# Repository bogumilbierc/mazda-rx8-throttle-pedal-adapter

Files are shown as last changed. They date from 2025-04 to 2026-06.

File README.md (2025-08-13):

# Mazda RX-8 throttle pedal to M113 ECU adapter

Mazda RX-8 throttle pedal adapter for Mercedes M113 ECU (M113 V8 swap into RX-8).

<!-- TOC -->
* [Mazda RX-8 throttle pedal to M113 ECU adapter](#mazda-rx-8-throttle-pedal-to-m113-ecu-adapter)
  * [OEM Pedals documentation](#oem-pedals-documentation)
  * [Adapter](#adapter)
    * [How it works](#how-it-works)
    * [Basic logic (runs in loop)](#basic-logic-runs-in-loop)
  * [Components](#components)
  * [Circuit diagram](#circuit-diagram)
  * [Assembled adapter](#assembled-adapter)
  * [Arduino IDE setup](#arduino-ide-setup)
  * [Adopting a similar solution for other swaps (different ECUs/pedals)](#adopting-a-similar-solution-for-other-swaps-different-ecuspedals)
<!-- TOC -->

## OEM Pedals documentation

- [RX-8 pedal](./docs/rx-8-pedal/rx-8-pedal.md)
- [M113 pedal](./docs/m113-pedal/m113-pedal.md)

## Adapter

### How it works

Mazda RX-8 pedal has two sensors (potentiometers) that have voltage offset between each other.

M113 pedal has two sensors (potentiometers) that have one sensor being 2*voltage of the other sensor.

Adapter reads the voltage from Mazda pedal, converts it to M113 voltage with DAC (for one sensor) and then takes output
from DAC and divides it by two using a simple resistor-based voltage divider for the other sensor.

### Basic logic (runs in loop)

1. Read voltages from both sensors on RX-8 pedal
2. Calculate percentage from both sensors
3. Validate if percentages are not out of sync (safety feature)
    - if they are, set the throttle limit to 30%
    - if they are not, clear the throttle limit
4. Set output for DAC (for "high" pedal)

## Components

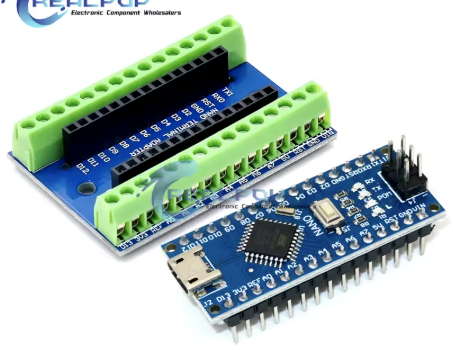
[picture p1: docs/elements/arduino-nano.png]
arduino nano
- Arduino Nano <br> 
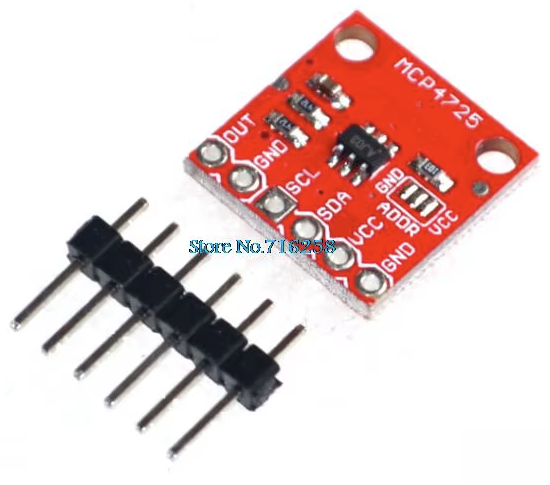
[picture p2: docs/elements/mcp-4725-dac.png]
mcp 4725 dac
- MCP4725 DAC <br> 
- RX-8 pedal plug
- two resistors for voltage divider (I choose 4.7 kOhm, but it does not really matter)
- some wires

## Circuit diagram

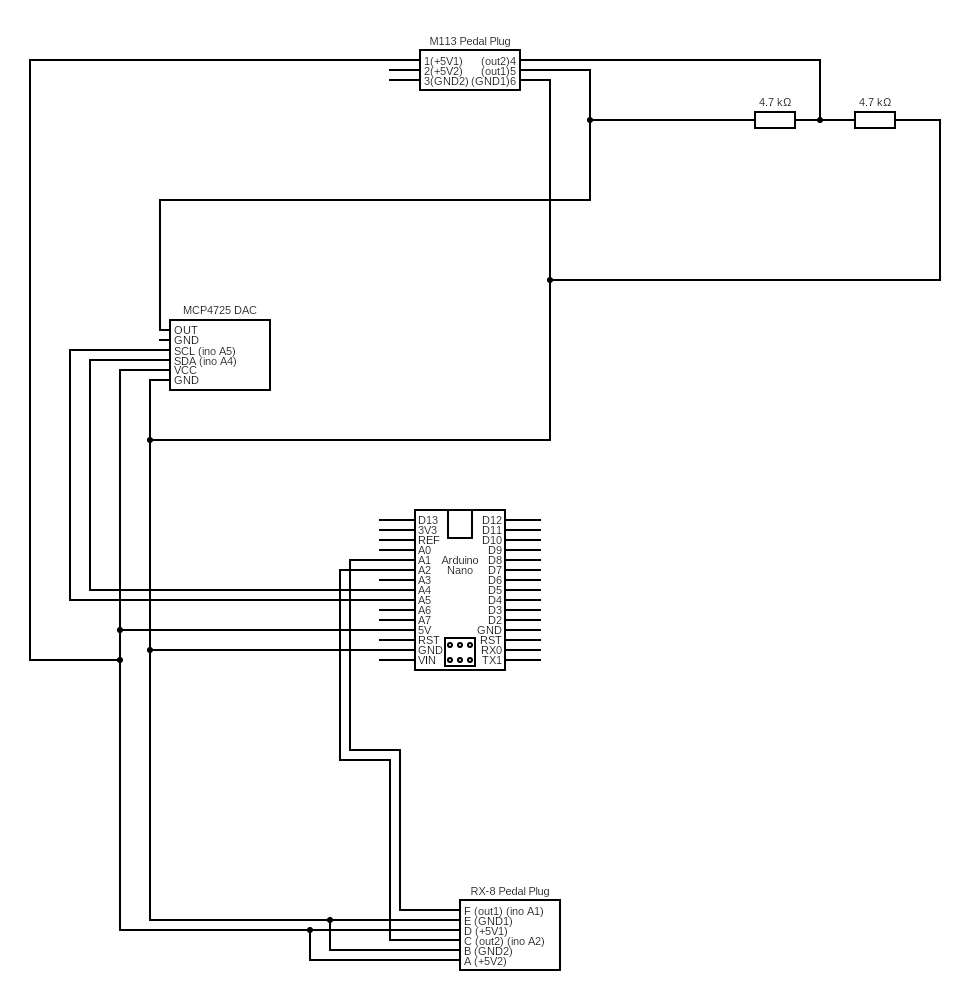
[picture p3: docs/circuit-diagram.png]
circuit diagram


Circuit was drawn using https://www.circuit-diagram.org/.

Source code for the diagram is located in [circuit cddx file](./docs/circuit.cddx)

## Assembled adapter

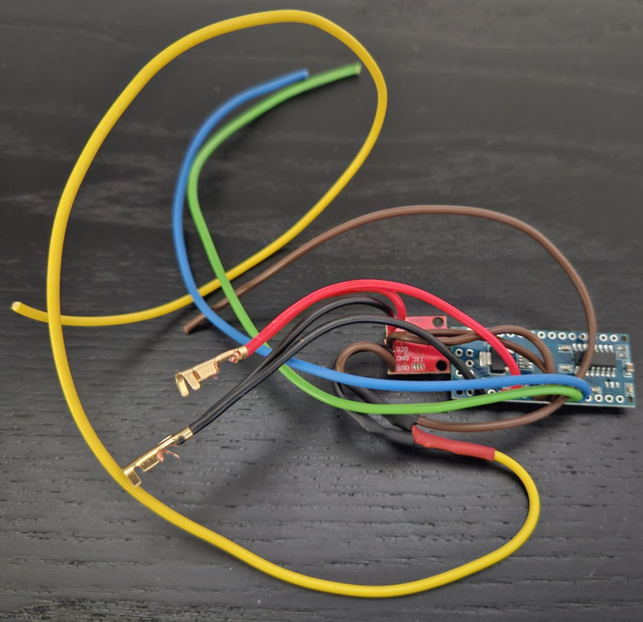
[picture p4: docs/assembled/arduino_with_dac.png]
arduino_with_dac


Note: This is from a previous version, I've later on decided to insert wires from the top, as it makes it easier to mount the assembly in the case.

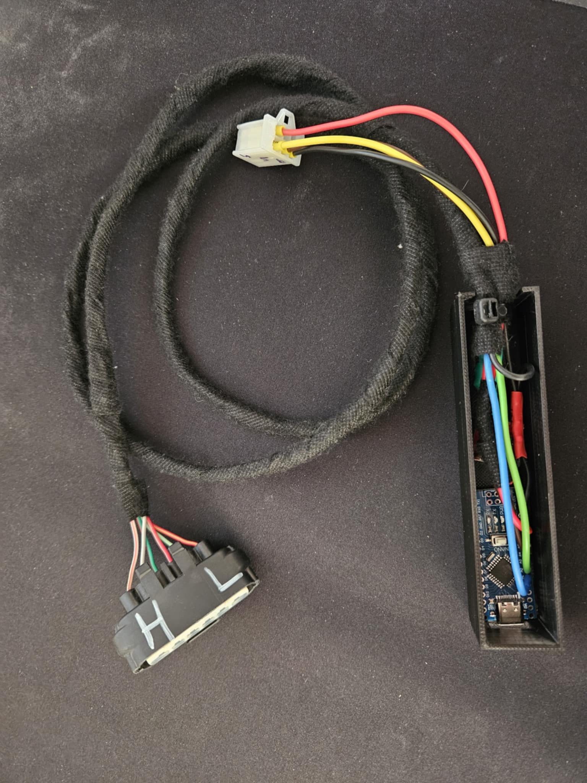
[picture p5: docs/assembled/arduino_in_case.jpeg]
arduino in case


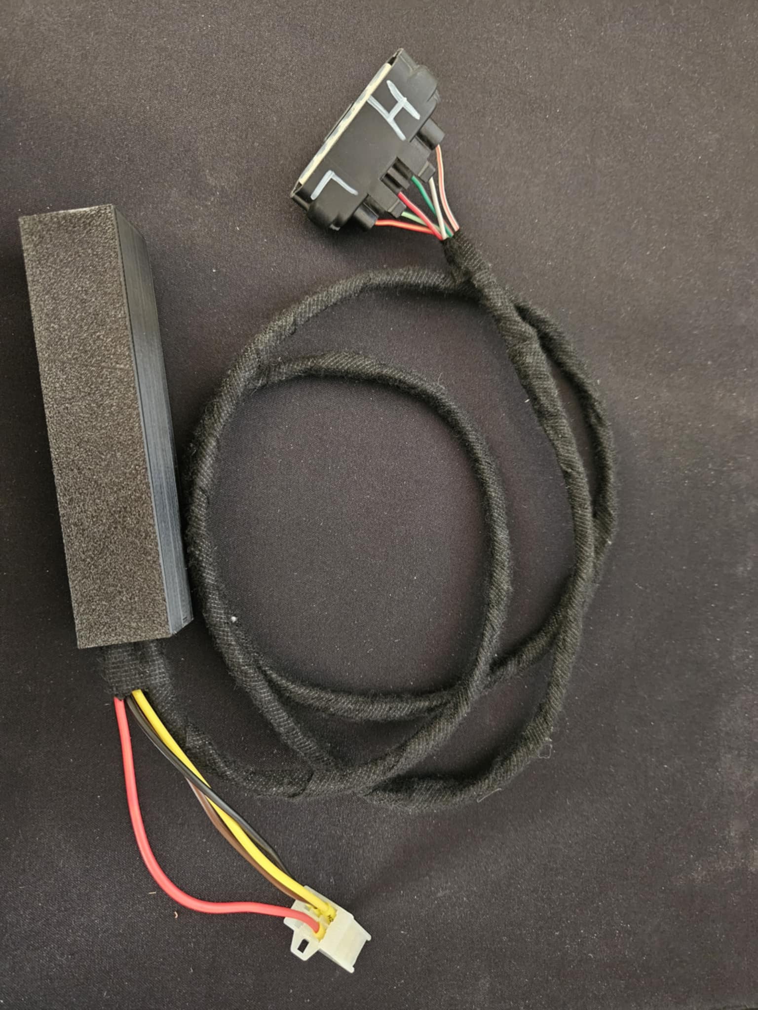
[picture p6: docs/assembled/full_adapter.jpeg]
full adapter


## Arduino IDE setup

- Install Adafruit_MCP4725 library
- Load project from `arduino/pedal_adapter/pedal_adapter.ino`

## Adopting a similar solution for other swaps (different ECUs/pedals)

If You have a different swap than M113 You will need to:

- read voltages from the throttle pedal
    - if they have the same logic as for mercedes (one is a multiplication of the other)
        - You need to recalculate DAC values using the script from "utils"
    - if they have different logic (offset, whatever)
        - You need to either:
            - use two DACs (easier but requires small code change)
            - use voltage subtractor (a bit more complex electronic wise, but no code changes required)

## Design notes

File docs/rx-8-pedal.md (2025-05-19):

# Mazda RX-8 Throttle pedal

## Pedal plug

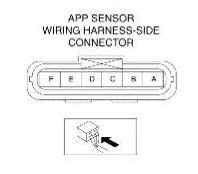
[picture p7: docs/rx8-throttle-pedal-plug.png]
pedal plug picture

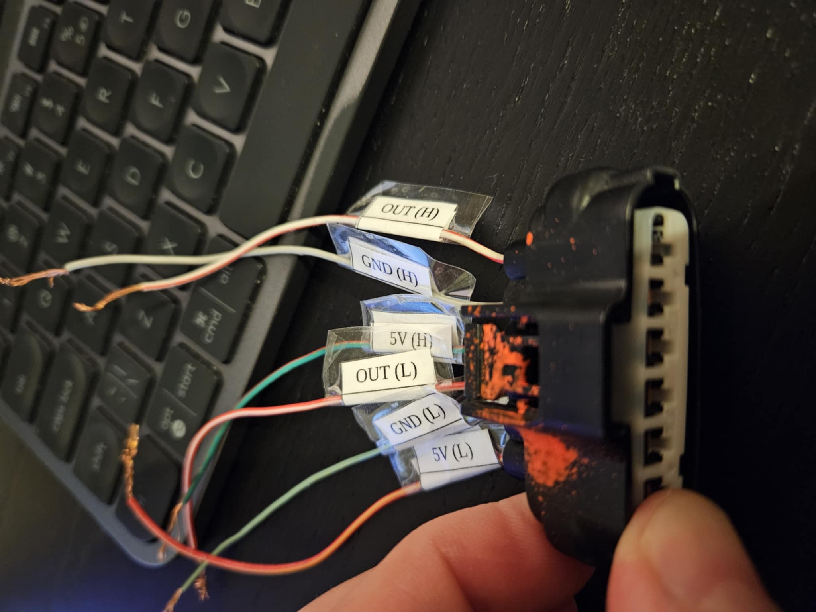
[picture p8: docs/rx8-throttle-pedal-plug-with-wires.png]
pedal plug with wires


Pins are numbered looking from the wiring side (back side of the plug).

## Plug pinout

| pin number | wire color | sensor | function |
|---|---|---|---|
| F | white-red | main (high) | sensor output |
| E | gray | main | GND |
| D | green-red | main | +5V |
| C | red-white | secondary (low) | sensor output |
| B | lightgreen-black | secondary | GND |
| A | red-yellow | secondary | +5V |

## Pedal voltages

Voltages captured using an external power supply and two multimeters.

| HIGH | LOW  | DIFF |
|---|---|---|
| 1,58 | 1,03 | 0,55 |
| 1,98 | 1,41 | 0,57 |
| 2,11 | 1,54 | 0,57 |
| 2,45 | 1,88 | 0,57 |
| 2,59 | 2,02 | 0,57 |
| 2,6  | 2,03 | 0,57 |
| 2,71 | 2,14 | 0,57 |
| 2,72 | 2,15 | 0,57 |
| 2,79 | 2,24 | 0,55 |
| 2,85 | 2,28 | 0,57 |
| 2,98 | 2,42 | 0,56 |
| 3,19 | 2,62 | 0,57 |
| 3,61 | 3,05 | 0,56 |
| 3,9  | 3,35 | 0,55 |

There is ~0.55 V of difference between two potentiometers in the pedal.

If we assume that we will divide pedal position into 100 steps, then each step will have ~0.02 voltage range.
This should be good enough for Arduino's ADC.

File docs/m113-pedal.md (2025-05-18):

# M113 Throttle pedal

## Pedal plug (pedal side)

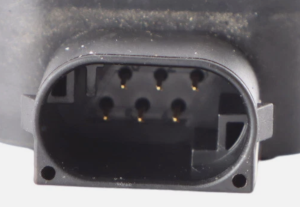
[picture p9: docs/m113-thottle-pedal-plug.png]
pedal plug picture


## Plug pinout

| pin number | sensor | function |
|---|---|---|
| 1 | main | +5V |
| 2 | secondary | +5V |
| 3 | secondary | GND |
| 4 | secondary (up to 2.5V) | sensor output |
| 5 | main(up to 5v) | sensor output |
| 6 | main | GND |

## ECU pinout

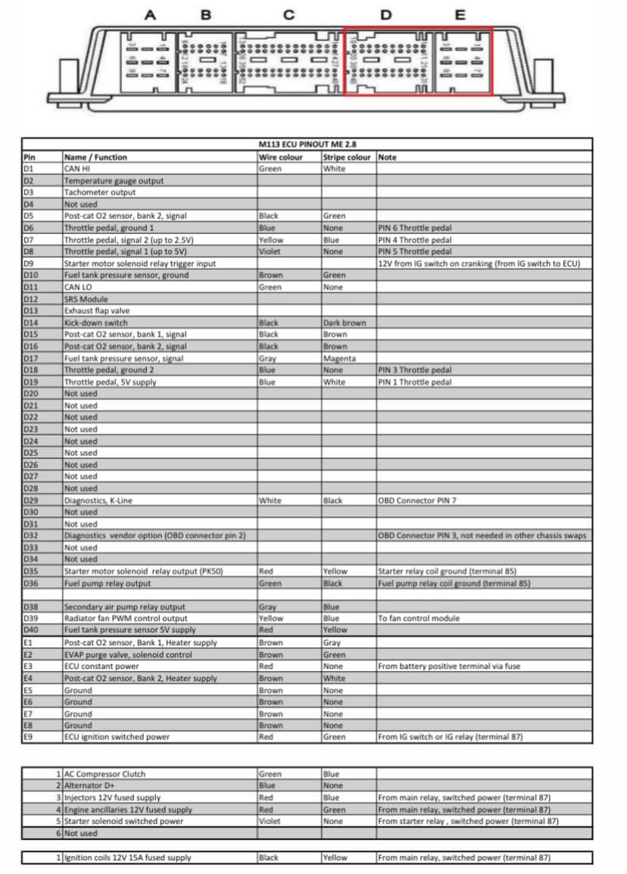
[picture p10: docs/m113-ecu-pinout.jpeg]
ecu pinout


## Pedal voltages

### Captured with multimeter

Voltages captured using an external power supply and two multimeters.

This not exactly `high=2*low`, probably due to using second-hand pedal that wasn't ideal.

| high | low  | diff | multiplier |
|---|---|---|---|
| 0.29 | 0.13 | 0.16 | 2.23076923076923 |
| 0.56 | 0.29 | 0.27 | 1.93103448275862 |
| 0.89 | 0.38 | 0.51 | 2.34210526315789 |
| 0.94 | 0.43 | 0.51 | 2.18604651162791 |
| 1.06 | 0.51 | 0.55 | 2.07843137254902 |
| 1.19 | 0.52 | 0.67 | 2.28846153846154 |
| 1.23 | 0.57 | 0.66 | 2.15789473684211 |
| 1.24 | 0.58 | 0.66 | 2.13793103448276 |
| 1.25 | 0.59 | 0.66 | 2.11864406779661 |
| 1.35 | 0.64 | 0.71 | 2.109375 |
| 1.4  | 0.65 | 0.75 | 2.15384615384615 |
| 1.57 | 0.75 | 0.82 | 2.09333333333333 |
| 1.62 | 0.77 | 0.85 | 2.1038961038961  |
| 1.77 | 0.84 | 0.93 | 2.10714285714286 |
| 1.94 | 0.93 | 1.01 | 2.08602150537634 |
| 2.04 | 1 | 1.04 | 2.04 |
| 2.19 | 1.06 | 1.13 | 2.06603773584906 |
| 2.31 | 1.15 | 1.16 | 2.00869565217391 |
| 2.56 | 1.24 | 1.32 | 2.06451612903226 |
| 2.86 | 1.39 | 1.47 | 2.05755395683453 |
| 3.19 | 1.53 | 1.66 | 2.08496732026144 |
| 4.07 | 1.95 | 2.12 | 2.08717948717949 |
| 4.27 | 2.09 | 2.18 | 2.04306220095694 |
| 4.39 | 2.27 | 2.12 | 1.93392070484582 |
| 4.68 | 2.32 | 2.36 | 2.01724137931034 |

### Captured via OBD

Voltages captured using DS150 clone.

This is much closer to `high=2*low`, probably safe to assume it is and take into consideration that pedal in the car was
not new either.

| high | low  | multiplier  |
| ---- | ---- | --- |
| 0,33 | 0,19 | 1,736842105 |
| 1,05 | 0,6  | 1,75 |
| 1,38 | 0,69 | 2 |
| 1,6  | 0,8  | 2 |
| 1,85 | 0,93 | 1,989247312 |
| 1,93 | 1,04 | 1,855769231 |
| 1,96 | 0,98 | 2 |
| 2,23 | 1,12 | 1,991071429 |
| 2,3  | 1,15 | 2 |
| 2,36 | 1,18 | 2 |
| 2,56 | 1,28 | 2 |
| 2,65 | 1,33 | 1,992481203 |
| 2,73 | 1,37 | 1,99270073  |
| 2,98 | 1,5  | 1,986666667 |
| 3,24 | 1,63 | 1,987730061 |
| 3,31 | 1,66 | 1,993975904 |
| 3,54 | 1,78 | 1,988764045 |
| 3,55 | 1,78 | 1,994382022 |
| 3,89 | 1,95 | 1,994871795 |
| 3,97 | 1,99 | 1,994974874 |
| 4,06 | 2,3  | 2 |
| 4,31 | 2,16 | 1,99537037  |
| 4,67 | 2,34 | 1,995726496 |

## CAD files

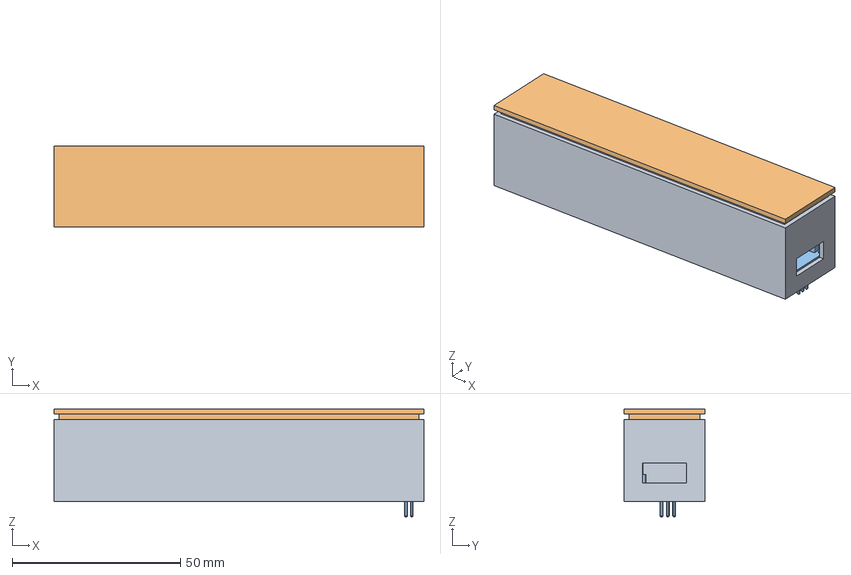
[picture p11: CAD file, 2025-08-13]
case/case_v2.FCStd
110.0 x 24.0 x 32.0 mm
MainCaseBody
TopCoverBody
Arduino v5

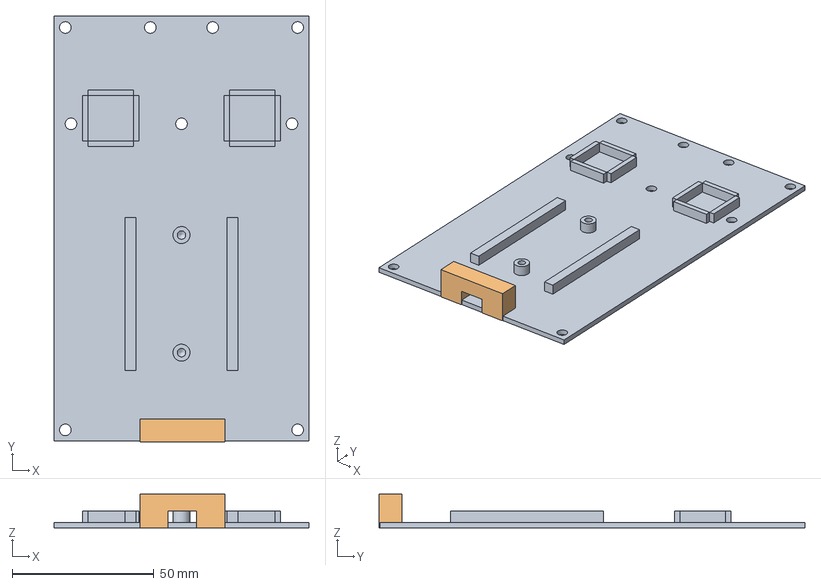
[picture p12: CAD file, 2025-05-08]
case/case_bottom_plate.FCStd
90.0 x 150.2 x 12.0 mm
BottomPlateBody
RX8PedalCablesTieDown

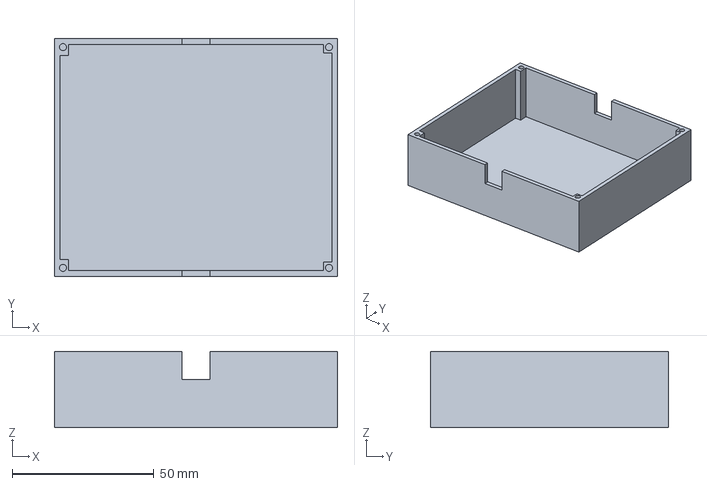
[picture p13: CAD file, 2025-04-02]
case/case_cover.FCStd
100.0 x 84.0 x 27.0 mm

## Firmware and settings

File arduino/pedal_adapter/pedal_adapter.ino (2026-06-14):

/**
* Mazda RX-8 Throttle Pedal Adapter
*
* Reads two redundant analog signals from an accelerator pedal position sensor,
* converts them to a throttle percentage (0-100%), and outputs a corresponding
* voltage via an MCP4725 I²C DAC to drive an M113 ECU throttle input.
*
* Safety features:
* - Dual-sensor cross-check: limits throttle to 30% if sensors disagree by >4%
* - Hardware watchdog (250ms): resets to idle on MCU hang
* - Output clamped to valid range to prevent out-of-bounds conditions
*
* Hardware: Arduino Nano V3 (ATmega328P), MCP4725 DAC
* Check README in main folder to verify wiring diagram
**/
#define DEBUG_ENABLED false
#define FASTADC true  // with fastadc (prescaler set to 16) it is around 3 times faster than on the standard Arduino setting (measured with loops of 1k invocations of ADC)

// defines for setting and clearing register bits
#ifndef cbi
#define cbi(sfr, bit) (_SFR_BYTE(sfr) &= ~_BV(bit))
#endif
#ifndef sbi
#define sbi(sfr, bit) (_SFR_BYTE(sfr) |= _BV(bit))
#endif


#include <Wire.h>
#include <avr/pgmspace.h>
#include <avr/wdt.h>
//MCP4725 library
#include <Adafruit_MCP4725.h>

// fractions generated with "utils/dac-voltages-generator.html"
const int FRACTIONS_FOR_M113_ECU[] PROGMEM = { 270, 303, 344, 376, 417, 450, 483, 524, 557, 598, 630, 663, 704, 737, 778, 811, 843, 884, 917, 958, 991, 1024, 1064, 1097, 1138, 1171, 1204, 1245, 1277, 1318, 1351, 1384, 1425, 1458, 1499, 1531, 1564, 1605, 1638, 1679, 1712, 1744, 1785, 1818, 1859, 1892, 1925, 1966, 1998, 2039, 2072, 2105, 2146, 2179, 2220, 2252, 2285, 2326, 2359, 2400, 2433, 2465, 2506, 2539, 2580, 2613, 2646, 2686, 2719, 2760, 2793, 2826, 2867, 2899, 2940, 2973, 3006, 3047, 3080, 3121, 3153, 3186, 3227, 3260, 3301, 3334, 3366, 3407, 3440, 3481, 3514, 3547, 3588, 3620, 3661, 3694, 3727, 3768, 3801, 3842, 3874 };

const int DAC_ADDRESS = 0x60;

const long MIN_LOW = 212;
const long MIN_HIGH = 323;

// range is (MAX-MIN) which is the same for both LOW and HIGH inputs
const int PEDAL_RANGE = 476;

// used to limit throttle / put adapter into safety mode in case sensors go out of sync
int THROTTLE_LIMIT = 100;

// used to speed up the code -> don't call DAC if same value is passed multiple times in a row
int lastValue = -1;

Adafruit_MCP4725 mcp4725;

void setup() {
  wdt_enable(WDTO_250MS);

#if FASTADC == true
  // set prescale to 16
  sbi(ADCSRA, ADPS2);
  cbi(ADCSRA, ADPS1);
  cbi(ADCSRA, ADPS0);
#endif

#if DEBUG_ENABLED == true
  Serial.begin(9600);
#endif

  // analogReference(EXTERNAL); // this should not matter since board is powered via 5V pin
  initializeDac();
}

void loop() {
  wdt_reset();

  int lowPercentage = readLowPedalPercentage();
  int highPercentage = readHighPedalPercentage();

  setThrottleLimit(lowPercentage, highPercentage);

  int calculatedAveragePercentage = (lowPercentage + highPercentage) / 2;

#if DEBUG_ENABLED == true
  Serial.print(F("ThrottlePos:: "));
  Serial.print(calculatedAveragePercentage);
  Serial.print(F(" low::"));
  Serial.print(lowPercentage);
  Serial.print(F(" high::"));
  Serial.println(highPercentage);
#endif

  calculatedAveragePercentage = constrain(calculatedAveragePercentage, 0, 100);

  setOutputValue(calculatedAveragePercentage);
}

void initializeDac() {
  bool initialized = mcp4725.begin(DAC_ADDRESS);
  Wire.setClock(400000); // Update I²C clock from 100 to 400 kHz
#if DEBUG_ENABLED == true
  Serial.print(F("DAC initialized: "));
  Serial.println(initialized);
#endif
  setOutputValue(0);  // set pedal to 0%
}

int readLowPedalPercentage() {
  int lowInput = analogRead(A2);
  long upperPart = (lowInput - MIN_LOW) * 100;
  return upperPart / PEDAL_RANGE;
}

int readHighPedalPercentage() {
  int highInput = analogRead(A1);
  long upperPart = (highInput - MIN_HIGH) * 100;
  return upperPart / PEDAL_RANGE;
}

void setThrottleLimit(int lowPercentage, int highPercentage) {
  if (abs(highPercentage - lowPercentage) > 4) {
    // todo: blink led, beep - they are out of sync
    THROTTLE_LIMIT = 30;
#if DEBUG_ENABLED == true
    Serial.println(F("Sensors are out of sync."));
#endif
  } else {
    THROTTLE_LIMIT = 100;
  }
}

void setOutputValue(int calculatedAveragePercentage) {
  int percentageToUse = min(calculatedAveragePercentage, THROTTLE_LIMIT);
  if (percentageToUse == lastValue) {
#if DEBUG_ENABLED == true
    Serial.println(F("Passed value is the same as previous value. Skipping DAC call."));
#endif
    return;
  }
  uint16_t dacValue = pgm_read_word(&FRACTIONS_FOR_M113_ECU[percentageToUse]);
  mcp4725.setVoltage(dacValue, false);
  lastValue = percentageToUse;
}

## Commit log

2025-03-16 Fix RX-8 pedal plug pinout, add colors to wires
2025-03-28 Add voltages read from rx-8 pedal.
2025-03-31 Add FreeCad project with case bottom plate
    [case_bottom_plate.FCStd]
2025-04-02 Add cover for case
    [case_cover.FCStd]
2025-05-07 Modify case bottom plate to fit one arduino and two DACs
    [case_bottom_plate.FCStd]
2025-05-07 Add tiedowns for rx8 pedal cables model
    [case_bottom_plate.FCStd]
2025-05-07 Add arduino throttle pedal readout code
2025-05-08 Make case for arduino bigger. make tiedown cutouts bigger, make holes tighter
    [case_bottom_plate.FCStd]
2025-05-19 refactor codel add throttle limit
2025-05-19 Fix pedal readout after refactor; Add util to calculate output voltage
    [rx8_throttle_pedal_readout.ino]
2025-05-19 Use Adafruit_MCP4725 library (as the other one does not work); Update readme
    [rx8_throttle_pedal_readout.ino]
2025-05-19 Rename arduino code
2025-05-19 Add circuit diagram
2025-05-20 Add circuit diagram source code
2025-05-20 Optimize calls to DAC - skip calls if same value is passed multiple times in a row
    [pedal_adapter.ino]
2025-05-21 add missing lastValue setter
    [pedal_adapter.ino]
2025-07-18 Add an assembled adapter picture to readme
2025-08-10 Add v2 of case for minimized design
    [case_v2.FCStd]
2025-08-11 Add cutouts for usb and transparent glass for LEDs
    [case_v2.FCStd]
2025-08-11 Make floor and walls thinner for the adapter case
    [case_v2.FCStd]
2025-08-11 Use fastADC / prescaler set to 16 for ADC
2025-08-11 Add top cover for case
    [case_v2.FCStd]
2025-08-13 Make case smaller for thin design of arduino
    [case_v2.FCStd]
2025-08-13 Add lid to case; Remove redundant window
    [case_v2.FCStd]
2026-05-24 Speed up DAC i2c bus
